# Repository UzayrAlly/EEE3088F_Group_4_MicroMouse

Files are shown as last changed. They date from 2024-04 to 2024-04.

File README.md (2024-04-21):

# EEE3088F_Group_4_MicroMouse
Micro-Mouse Sensing Subsystem

This repository contains the design documentation and testing procedures for the sensing subsystem of the Micro-Mouse project. The sensing subsystem serves as the "eyes" of the Micro-Mouse, detecting walls within a maze environment using infrared light and providing signals for navigation.

Contents:

Design Decisions: Discusses the initial circuit design, component selection, evaluation, and final design of the sensing module. It outlines the rationale behind component choices and design modifications.
Failure Management: Describes the processes implemented for failure management in PCB design, including Electrical Rule Check (ERC), Design Rule Check (DRC), Design for Manufacturing (DFM), troubleshooting design, and circuit testing.
System Integration and Interfacing: Details the interfacing specifications and connections of the sensing subsystem with other components of the Micro-Mouse project. Includes an interfacing diagram and table describing the connections.
Acceptance Testing: Provides a comprehensive overview of acceptance tests conducted to verify that all components function as expected and meet requirements and specifications. Each test is described along with its testing procedure and pass/fail criteria.

Repository Structure:

Data sheets: data sheets for components.
Schematics: Includes schematic diagrams of the initial and final circuit designs for the sensing module.
PCB production files: includes items needed to manufacture the board

Usage:

This repository serves as a reference for understanding the design and testing procedures of the Micro-Mouse sensing subsystem. Developers and engineers can utilize the documentation and schematics for further development or troubleshooting.

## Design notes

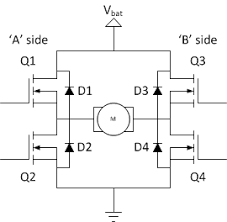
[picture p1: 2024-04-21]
Power_Subsystem_ALLUZA002/Datasheets/Motor Drivers/H-BridgeSchematic.png

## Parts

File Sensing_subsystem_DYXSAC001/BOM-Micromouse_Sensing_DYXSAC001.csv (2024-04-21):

Comment | Designator | Footprint | LCSC
MMBT3904 | Q1,Q3,Q4 | SOT-23 | C20526
47 | R1,R10,R13,R5,R8,R9 | R_0603_1608Metric | C23182
680 | R11,R3,R6 | R_0603_1608Metric | C23228
820 | R12,R2,R7 | R_0603_1608Metric | C23253
8.2k | R14,R15,R4 | R_0603_1608Metric | C25981
SFH309 | Q2,Q5,Q6 | LED_D3.0mm_Horizontal_O1.27mm_Z2.0mm_Clear | C2900253
TSAL6200 | D1,D2,D3,D4,D5,D6 | LED_D5.0mm_Horizontal_O1.27mm_Z3.0mm_IRBlack | C55528
22u | C2,C4,C6 | C_0603_1608Metric | C59461
10u | C1,C3,C5 | C_0603_1608Metric | C96446

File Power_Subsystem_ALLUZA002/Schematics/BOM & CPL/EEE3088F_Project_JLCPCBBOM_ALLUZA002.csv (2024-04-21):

Comment | Designator | Footprint | LCSC
10uF | C1,C2,C4 | C1206 | C13585
TP4056 | U2 | ESOP-8_L4.9-W3.9-P1.27-LS6.0-BL-EP | C16581
22k | R7 | R0805 | C17560
1k | R1,R2,R3,R4 | R0603 | C21190
RED | D2 | LED0603-RD | C2286
GREEN | D1 | LED0805-R-RD | C2297
2.2uF | C3,C5 | C0603 | C23630
SS12D10G4_071 | U1 | SW-TH_SHOU-HAN_SS12D10G4 | C2887259
3k | R5 | R0603 | C4211
DRV8833PWP | U3 | TSSOP-16_L5.0-W4.4-P0.65-LS6.4-BL-EP | C50506

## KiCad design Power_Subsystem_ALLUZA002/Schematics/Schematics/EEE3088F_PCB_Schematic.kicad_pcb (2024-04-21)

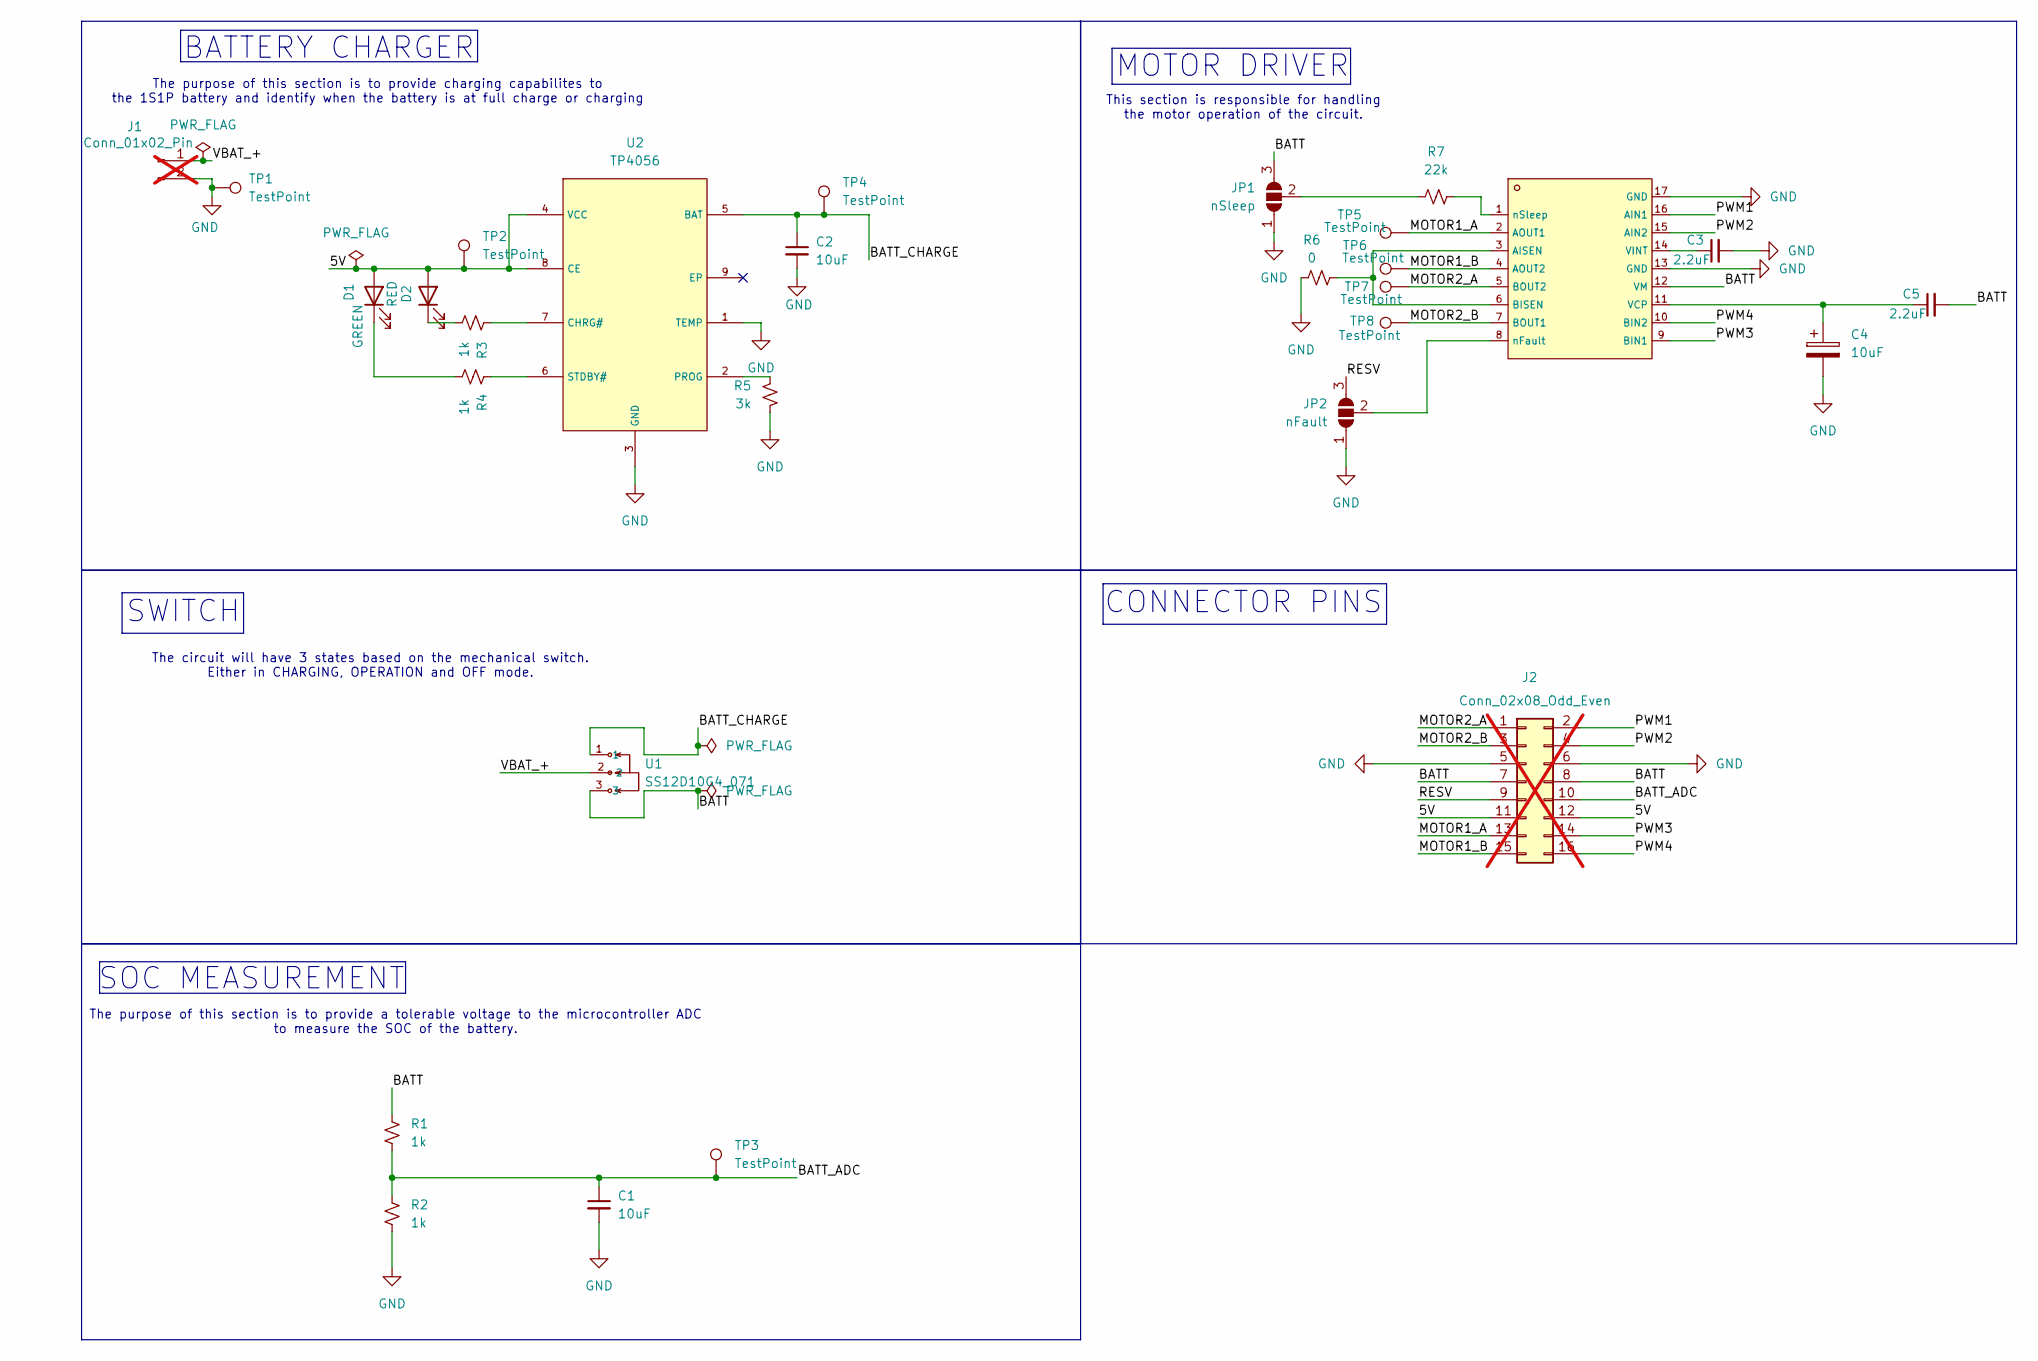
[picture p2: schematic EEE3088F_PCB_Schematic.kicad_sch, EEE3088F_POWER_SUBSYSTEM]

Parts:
C1, C2, C4: 10uF; C1206
C3, C5: 2.2uF; C0603
D1: GREEN; LED0805-R-RD
D2: RED; LED0603-RD
J1: Conn_01x02_Pin; PinHeader_1x02_P2.00mm_Vertical; not fitted
J2: Conn_02x08_Odd_Even; PinHeader_2x08_P2.54mm_Vertical; not fitted
JP1: nSleep; SolderJumper-3_P1.3mm_Open_RoundedPad1.0x1.5mm_NumberLabels
JP2: nFault; SolderJumper-3_P1.3mm_Open_RoundedPad1.0x1.5mm_NumberLabels
R1, R2, R3, R4: 1k; R0603
R5: 3k; R0603
R6: 0; R0603
R7: 22k; R0805
TP1, TP2, TP3, TP4, TP5, TP6, TP7, TP8: TestPoint; TestPoint_Loop_D1.80mm_Drill1.0mm_Beaded
U1: SS12D10G4_071; SW-TH_SHOU-HAN_SS12D10G4; LCSC C2887259
U2: TP4056; ESOP-8_L4.9-W3.9-P1.27-LS6.0-BL-EP; LCSC C16581
U3: DRV8833PWP; TSSOP-16_L5.0-W4.4-P0.65-LS6.4-BL-EP; LCSC C50506

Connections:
/5V: D1.2 (A), D2.2 (A), J2.11, J2.12, TP2.1, U2.4 (VCC), U2.8 (CE)
/BATT: C5.2, J2.7, J2.8, JP1.3 (B), R1.1, U1.3, U3.12 (VM)
/BATT_ADC: C1.1, J2.10, R1.2, R2.1, TP3.1
/BATT_CHARGE: C2.1, TP4.1, U1.1, U2.5 (BAT)
/MOTOR1_A: J2.13, TP5.1, U3.2 (AOUT1)
/MOTOR1_B: J2.15, TP6.1, U3.4 (AOUT2)
/MOTOR2_A: J2.1, TP7.1, U3.5 (BOUT2)
/MOTOR2_B: J2.3, TP8.1, U3.7 (BOUT1)
/PWM1: J2.2, U3.16 (AIN1)
/PWM2: J2.4, U3.15 (AIN2)
/PWM3: J2.14, U3.9 (BIN1)
/PWM4: J2.16, U3.10 (BIN2)
/RESV: J2.9, JP2.3 (B)
/VBAT_+: J1.1, U1.2
GND: C1.2, C2.2, C3.2, C4.2, J1.2, J2.5, J2.6, JP1.1 (A), JP2.1 (A), R2.2, R5.1, R6.1, TP1.1, U2.1 (TEMP), U2.3 (GND), U3.13 (GND), U3.17 (GND)
unnamed: D1.1 (K), R4.1
unnamed: D2.1 (K), R3.1
unnamed: JP1.2 (C), R7.1
unnamed: JP2.2 (C), U3.8 (nFault)
unnamed: R3.2, U2.7 (CHRG#)
unnamed: R5.2, U2.2 (PROG)
unnamed: R4.2, U2.6 (STDBY#)
unnamed: R6.2, U3.3 (AISEN), U3.6 (BISEN)
unnamed: C4.1, C5.1, U3.11 (VCP)
unnamed: C3.1, U3.14 (VINT)
unnamed: R7.2, U3.1 (nSleep)

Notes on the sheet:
MOTOR DRIVER
BATTERY CHARGER
SWITCH
The circuit will have 3 states based on the mechanical switch. Either in CHARGING, OPERATION and OFF mode.
SOC MEASUREMENT
The purpose of this section is to provide charging capabilites to the 1S1P battery and identify when the battery is at full charge or charging
The purpose of this section is to provide a tolerable voltage to the microcontroller ADC to measure the SOC of the battery.
CONNECTOR PINS
This section is responsible for handling the motor operation of the circuit.

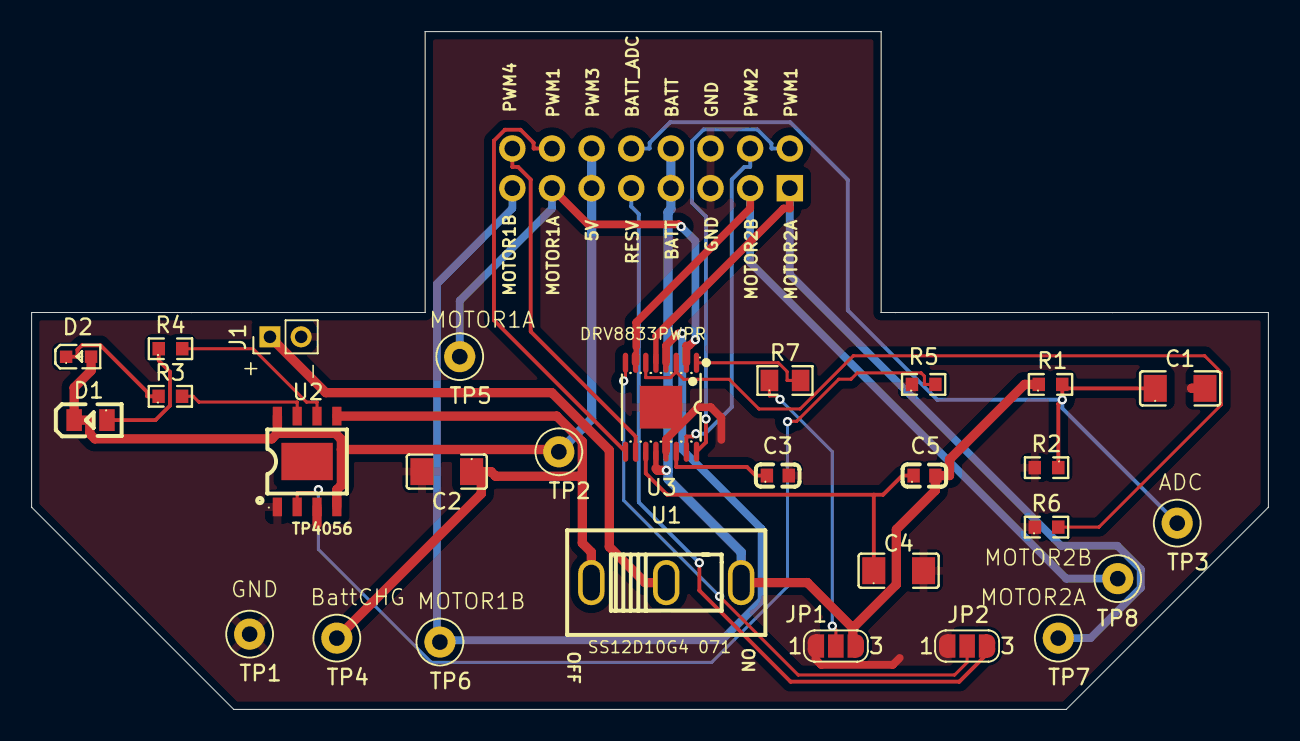
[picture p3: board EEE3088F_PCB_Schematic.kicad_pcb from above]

Board: 2 copper layers, 79.2 x 43.4 mm, 29 parts (1 on the bottom side), 26 nets.

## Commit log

2024-04-21 added PCB production files produced by the JLCPCB.
2024-04-21 Production files for sensing PCB
    [BOM-Micromouse_Sensing_DYXSAC001.csv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]
2024-04-21 PCB production files generated by JLCPCB
    [BOM-Micromouse_Sensing_DYXSAC001.csv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]
